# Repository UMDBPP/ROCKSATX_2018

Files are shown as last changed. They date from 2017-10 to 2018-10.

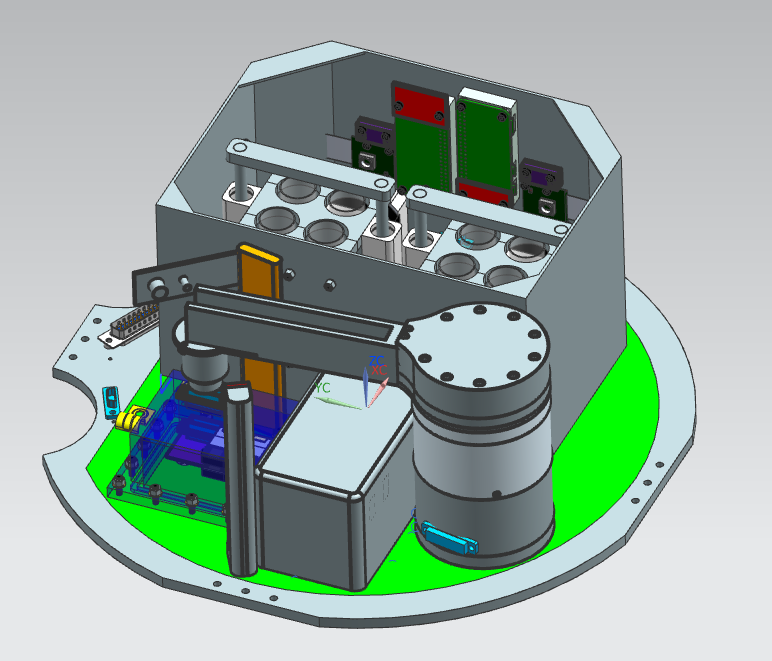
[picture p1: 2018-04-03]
CAD/CAD Renders/Opqaue Full Assembly ISTR.PNG

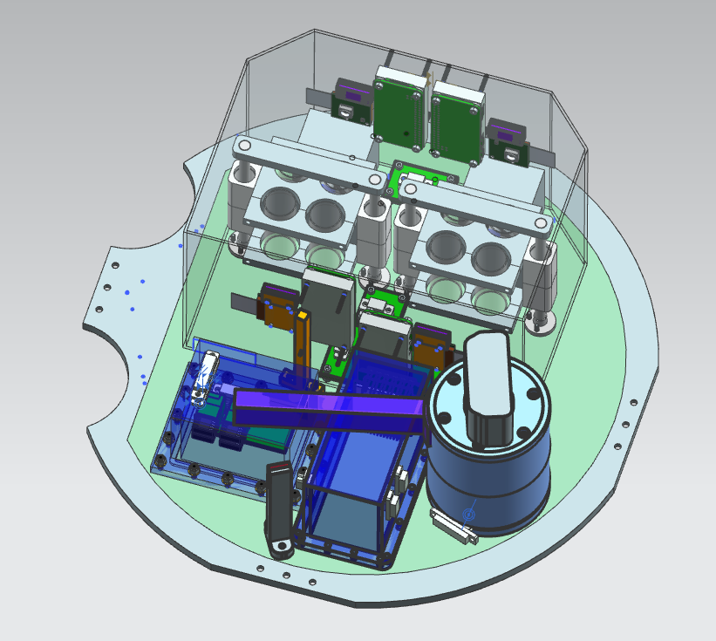
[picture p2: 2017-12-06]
CAD/CAD Renders/Full Assembly.PNG

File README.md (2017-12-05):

# ROCKSATX_2018
BPP 2018 Rocksat - X

Payload: TERP (Tribocharging Experiment and Robotic Performance)

Contains two experiments: STAR and SCAMP

## STAR
Stratification and Tribocharging Analysis of Regolith (STAR)

## SCAMP
Space Characterization and Assessment of Manipulator Performance

# Organization
CAD/: All mechanical design files (CAD)

Payload_Integration/:  Files documenting external interfaces of TERP

SCAMP/: SCAMP-specific design files

STAR/: STAR-specific design files

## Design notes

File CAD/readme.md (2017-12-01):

Top level assembly is: TERP_Payload.prt

Do not commit files with random numbers at the end. Do not use spaces in filenames.

To load assembly. 

* Open NX but not the assembly.
* Open assembly load options. Under Load, selected "From Search Folders"
* Under "Add folder to search", click browse, and select each subfolder in turn
* Click ok
* Release the assembly

This process only needs to be done on each users machine and every time a new folder is added.

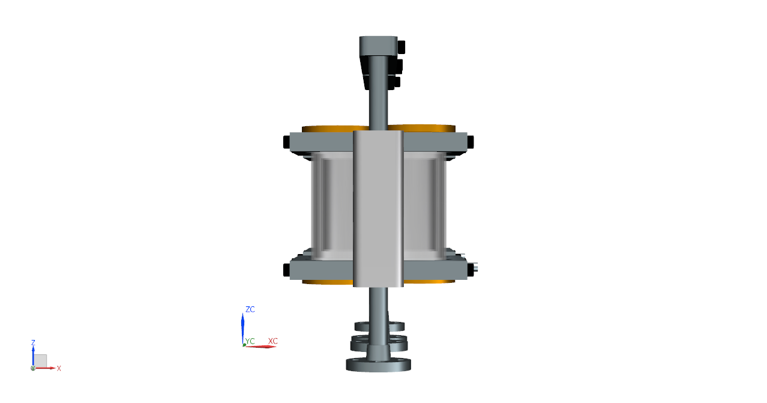
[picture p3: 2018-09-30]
CAD/CAD Renders/Shaker_rack_005.png

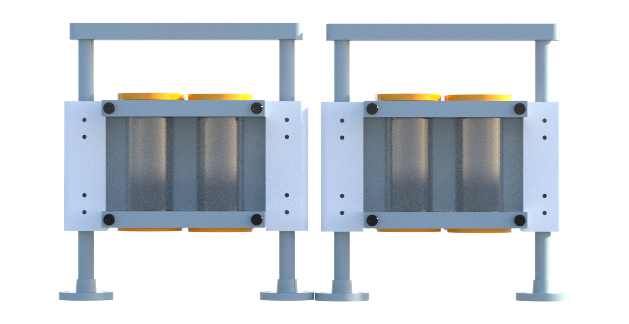
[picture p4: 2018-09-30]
CAD/CAD Renders/shaker_rack_008.png

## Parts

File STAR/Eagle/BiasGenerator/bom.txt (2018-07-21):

Partlist exported from D:/Joseph/Documents/School/College/Clubs/RockSatX/2017-2018/GIT/ROCKSATX_2018/STAR/Eagle/BiasGenerator/bias_generator.sch at 7/8/2018 3:00 PM

Qty Value             Device            Package       Parts           Description                                
2   .1uF              C-USC0603         C0603         C_GND, C_VCC    CAPACITOR, American symbol
CL10B104KB8NNNC          
1   1.5k              R-US_R2512        R2512         R_LTOUT         RESISTOR, American symbol                  
35221K5FT
1   10uF              CAPACITOR2-J-LEAD 2J-LEAD       C_LTOUT                                                    
CKG57NX7R2A106M500JH
1   1M                R-US_R0603        R0603         R_LAD1          RESISTOR, American symbol                  
ERJ-3GEYJ105V
2   1uF               CAPACITORC0603    0603          C_LTIN, C_LTREQ                                            
CL10A105KB8NNNC
2   20k               R-US_R0603        R0603         R_POT1          RESISTOR, American symbol                  
RMCF0603JT20K0
1   3269W-1-503LF     3269W-1-503LF     POTENTIOMETER R_POT2          Bourns Inc 50k Potentiometer 3269W-1-503LF 
1   33k               R-US_R0603        R0603         R_LAD2          RESISTOR, American symbol                  
1   4.7pF             CAPACITORC0603    0603          C_LAD                                                      
06032U4R7BAT2A
1   402k              R-US_R0603        R0603         R_DIV1          RESISTOR, American symbol                  
ERJ-3EKF4023V
1   52.6              R-US_R0603        R0603         R_LAD3          RESISTOR, American symbol                  
2   82nH              L-US              C0603         L_VCC, L_VOUT   INDUCTOR, American symbol                  
AIML-0603-82NK-T
1   AMC1311-Q1        AMC1311-Q1        SOIC8         ISO                                                        
1   ASPI-4020S-100M-T ASPI-4020S-100M-T 4MM           L_LT                                                       
1   DFT7160-105B      DFT7160-105B      DFT7160       CHOKE                                                      
1   J30J-9J30         J30J-9J30         ZKN-9-J30     J1                                                         
1   LT8330            LT8330            8-DFN         SWITCH                                                     
1   NCV4274ADT50RKG   NCV4274ADT50RKG   DPAK          REG                                                        
1   PMEG6010CEJ       SCHOTTKYSOD323    SOD323        D_LT

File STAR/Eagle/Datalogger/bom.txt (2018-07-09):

Partlist exported from C:/UMD/BPP/ROCKSAT X/2018/ROCKSATX_2018/STAR/Eagle/Datalogger/datalogger.sch at 7/8/2018 11:54

Qty Value        Device       Package         Parts               Description                
5   0.1uF        C-USC0603    C0603           C1, C3, C6, C7, C9  CAPACITOR, American symbol 
5   10nF         C-USC0603    C0603           C2, C4, C5, C8, C10 CAPACITOR, American symbol 
1   1M           R-US_R0603   R0603           R2                  RESISTOR, American symbol  
1   J30J-25      J30J-25      ZKN-25          J1                                             
1   MICRO_SD     MICRO_SD     MICRO_SD_HINGED U$1                                            
1   SSL.3IN_SILK SSL.3IN_SILK SSL_SILK_.3IN   GND1                                           
2   USB_A        USB_A        USB_A           U$2, U$3

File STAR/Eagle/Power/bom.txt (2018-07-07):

Partlist exported from C:/UMD/BPP/ROCKSAT X/2018/ROCKSATX_2018/STAR/Eagle/Power/Power.sch at 7/7/2018 15:11

Qty Value              Device             Package  Parts                   Description                
3   .1 uF              C-USC0603          C0603    C7, C8, C9              CAPACITOR, American symbol 
3   .18 uF             C-USC0603          C0603    C10, C11, C12           CAPACITOR, American symbol 
3   10 uF              C-USC0603          C0603    C13, C14, C15           CAPACITOR, American symbol 
3   10 uF              C-USC1210          C1210    C1, C2, C3              CAPACITOR, American symbol 
3   13.3k              R-US_R0603         R0603    R5, R7, R9              RESISTOR, American symbol  
5   1410J0500404MXTE03 1410J0500404MXTE03 1410     U$3, U$4, U$5, U$6, U$7                            
1   199.5k             R-US_R0603         R0603    R4                      RESISTOR, American symbol  
5   1nF                C-USC0603          C0603    C17, C19, C21, C23, C25 CAPACITOR, American symbol 
3   2.2 uF             C-USC1210          C1210    C4, C5, C6              CAPACITOR, American symbol 
3   23.2k              R-US_R0603         R0603    R1, R2, R3              RESISTOR, American symbol  
1   3.7u               7443551370         1365     L3                                                 
1   45.2k              R-US_R0603         R0603    R8                      RESISTOR, American symbol  
1   5.5u               744325550          1050     L2                                                 
5   744029000068       744029000068       2813     L4, L5, L6, L7, L8                                 
1   75.4k              R-US_R0603         R0603    R6                      RESISTOR, American symbol  
1   9.7u               744314101          7050     L1                                                 
2   DFT7160-105B       DFT7160-105B       DFT7160  U$1, U$2                                           
3   DO-214AC           DO-214AC           DO-214AC D1, D2, D3                                         
1   J30J-25            J30J-25            ZKN-25   J1                                                 
3   LMR16020           LMR16020           SO8      U1, U2, U3

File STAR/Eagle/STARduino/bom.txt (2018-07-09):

Partlist exported from C:/UMD/BPP/ROCKSAT X/2018/ROCKSATX_2018/STAR/Eagle/STARduino/starduino.sch at 7/8/2018 9:45

Qty Value                   Device                 Package         Parts                                                    Description                MANUFACTURER_PART_NUMBER VENDOR           
1                           JUMPER-2PTH            1X02            JP2                                                      Jumper                                                               
1                           PINHD-2X3              2X03            JP3                                                      PIN HEADER                                                           
1                           PINHD-2X5              2X05            JP1                                                      PIN HEADER                                                           
13  100nF                   C-USC0603              C0603           C1, C2, C3, C4, C7, C8, C9, C12, C13, C14, C16, C18, C20 CAPACITOR, American symbol                                           
1   100pF                   C-USC0603              C0603           C19                                                      CAPACITOR, American symbol                                           
2   10k                     R-US_R0603             R0603           R1, R2                                                   RESISTOR, American symbol                                            
2   10uF                    C-USC0603              C0603           C6, C15                                                  CAPACITOR, American symbol                                           
1   1nF                     C-USC0603              C0603           C17                                                      CAPACITOR, American symbol                                           
1   1uF                     C-USC0603              C0603           C5                                                       CAPACITOR, American symbol                                           
1   220k                    R-US_R0603             R0603           R8                                                       RESISTOR, American symbol                                            
1   220nF                   C-USC0603              C0603           C21                                                      CAPACITOR, American symbol                                           
1   3.6k                    R-US_R0603             R0603           R5                                                       RESISTOR, American symbol                                            
1   330                     R-US_R0603             R0603           R4                                                       RESISTOR, American symbol                                            
3   4.7k                    R-US_R0603             R0603           R3, R9, R10                                              RESISTOR, American symbol                                            
1   4.7k                    RESISTOR-ARRAY0603-ARV 0603-ARV        R7                                                       Array Chip Resistor                                                  
1   6.8k                    R-US_R0603             R0603           R6                                                       RESISTOR, American symbol                                            
2   6.8pF                   C-USC0603              C0603           C10, C11                                                 CAPACITOR, American symbol                                           
1   ABS07AIG-32.768KHZ-1-T  ABS07AIG-32.768KHZ-1-T 2-SMD           XTAL1                                                                                                                         
1   ADXL375BCCZ             ADXL375BCCZ            LGA-14          U8                                                                                                                            
1   ATSAMD21G18             ATSAMD21G18            48-TQFP         U2                                                                                                                            
2   BLM18KG221BH1D          FERRITE_BEAD-0603      0603            FB1, FB2                                                                                                                      
1   BMX055                  BMX055                 LGA-20          U7                                                                                                                            
1   CC2                     CC2                    CC2             U11                                                                                                                           
1   CR1025                  CR1025                 CR1025          B1                                                                                                                            
1   DS3231MZ+               DS3231MZ+              SOIC-8          U5                                                                                                                            
1   FODM8061-D              FODM8061-D             SO5             U$1                                                                                                                           
1   J30J-9J30J              J30J-9J30J             ZKN-9           J1                                                                                                                            
1   MAX31725MTA+            MAX31725MTA+           DFN-8           U3                                                                                                                            
1   MC14504BDTG             MC14504BDTG            TSSOP16         U6                                                                                                                            
1   MC74VHC1GT125           MC74VHC1GT125          SC-70-5         U4                                                                                                                            
1   PCA9306DCT              PCA9306DCT             SSOP8           U10                                                                                                                           
1   PCA9515A                PCA9515A               TSSOP8          U1                                                                                                                            
1   SSCMNNN015PA2A3         SSCMNNN015PA2A3        HSC-SMT-8       U12                                                                                                                           
1   SSL.3IN_SILK            SSL.3IN_SILK           SSL_SILK_.3IN   IMAG1                                                                                                                         
1   STAR                    STAR                   STAR_.3IN       IMAG2                                                                                                                         
1   TCA9535_RTW_24          TCA9535_RTW_24         RTW24_2P45X2P45 U9                                                                                  tca9535_rtw_24           Texas Instruments

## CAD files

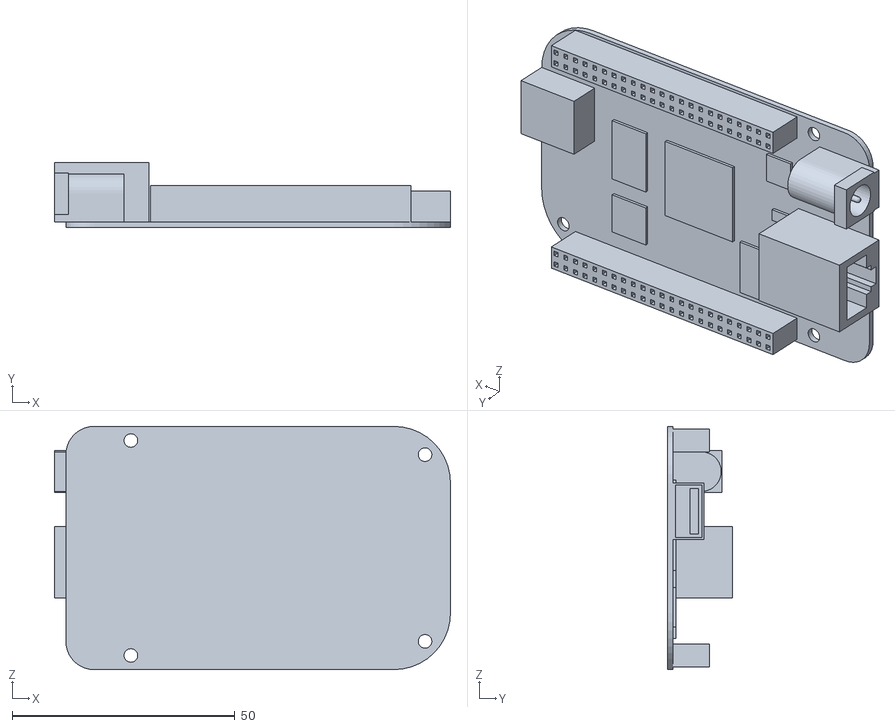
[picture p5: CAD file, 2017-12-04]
CAD/Beaglebone.stl
88.9 x 14.6 x 54.6

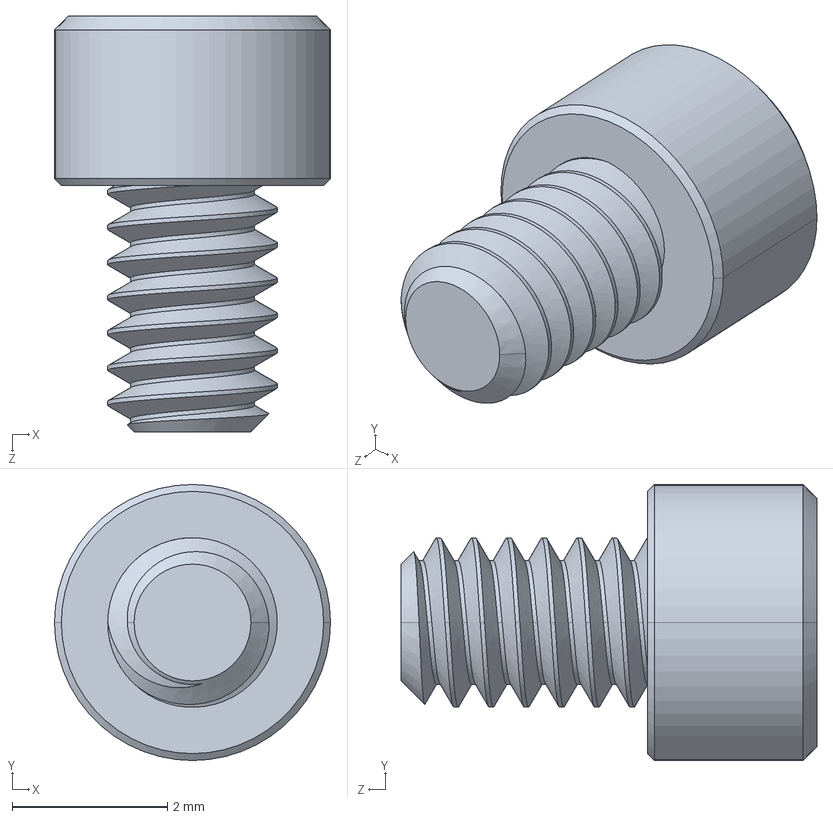
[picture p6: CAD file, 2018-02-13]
CAD/SCAMP V4.1/074.STEP
3.56 x 3.56 x 5.36 mm

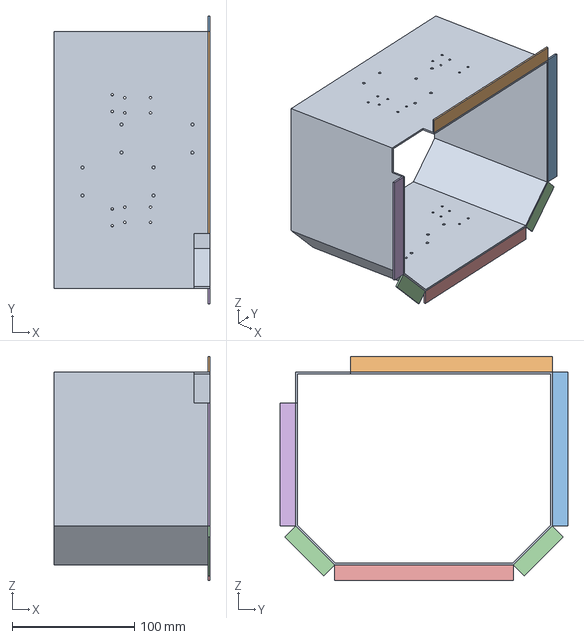
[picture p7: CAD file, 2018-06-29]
CAD/STEP/new_sunshade.stp
127.0 x 235.0 x 182.9 mm

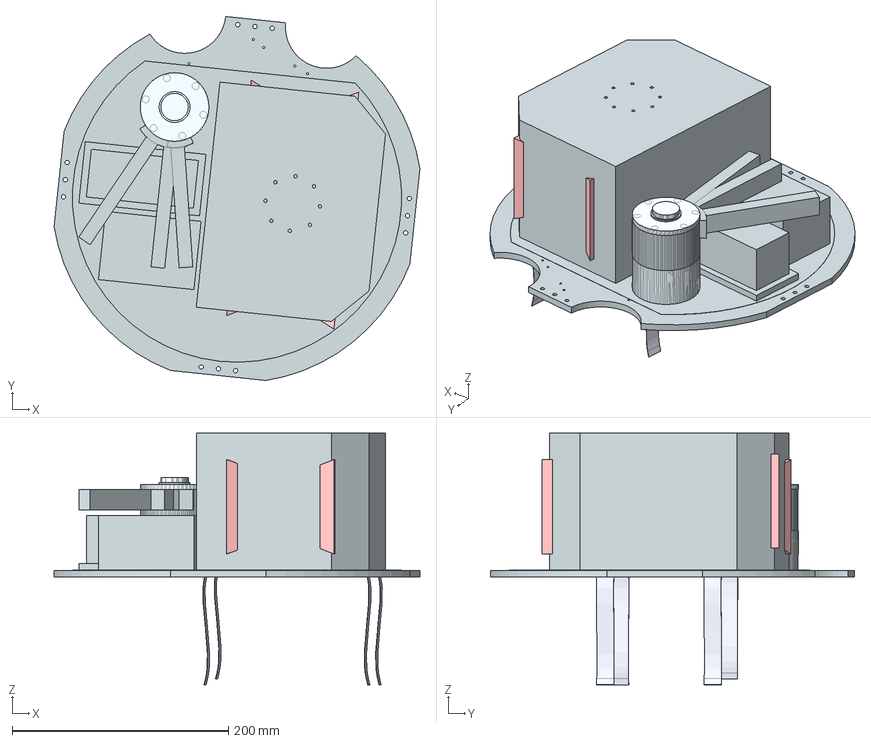
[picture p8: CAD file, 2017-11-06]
CAD/PDR_Plate_Layout.stp
338.7 x 337.0 x 233.0 mm
Electronics Box V2503
OVA5647_Lens_FOV x 4
newerbox448
new sunshade363486
PayloadSA218485
BasePlate (1)484
bearing holder473 x 8
tubeholderbase2472 x 2
test_tube482 x 8
slide rod481 x 4
rod_holder480 x 2
End Effector V3479 x 3
Pitch Motor Housing V281478 x 2
Motor End Cover444 x 2
Central Housing445 x 2
siliconbacking x 4
OVA5647_Pigtail486 x 4
OVA5647_IR-Glas485 x 4
OVA5647_Housing484 x 4
OVA5647483 x 4
RasPi_Camera_Board489 x 4
holderhalf2464 x 6
holderhalf463 x 2
link_arm x 2
shaker_disk x 2
Shaker_motor x 2

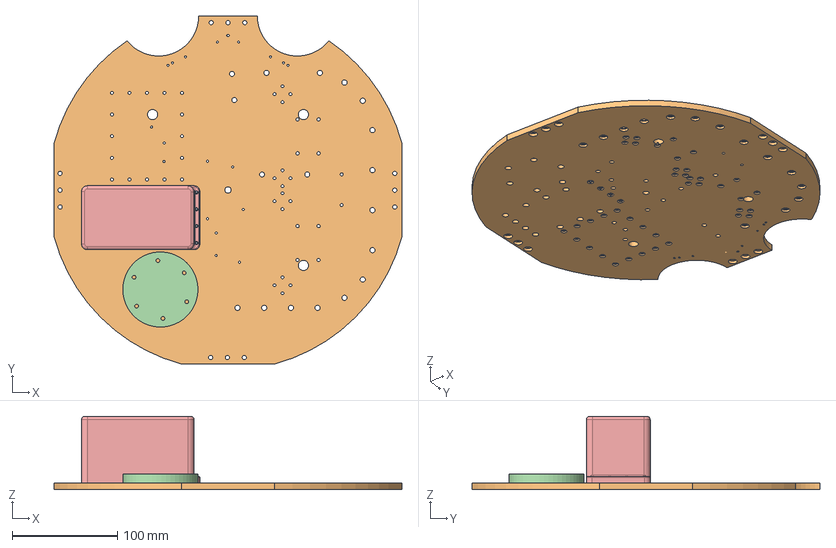
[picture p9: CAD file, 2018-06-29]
CAD/STEP/BasePlate2.stp
331.2 x 331.2 x 69.7 mm
106_step x 4

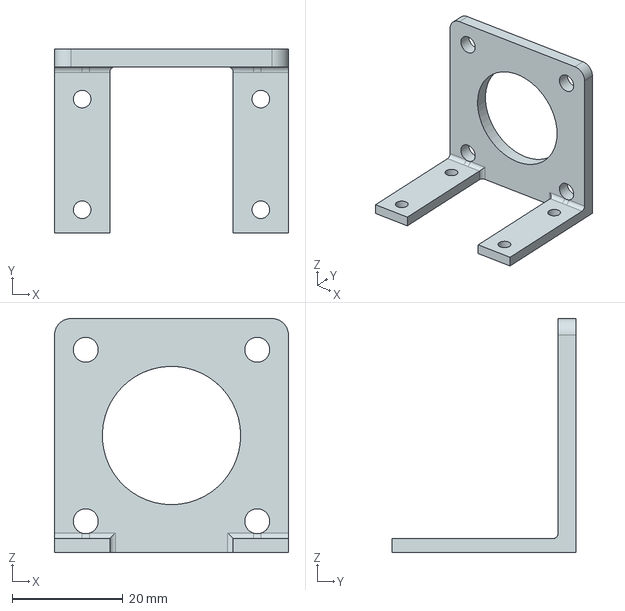
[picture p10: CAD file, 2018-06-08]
CAD/STEP/motor holder.stp
42.3 x 33.2 x 42.3 mm

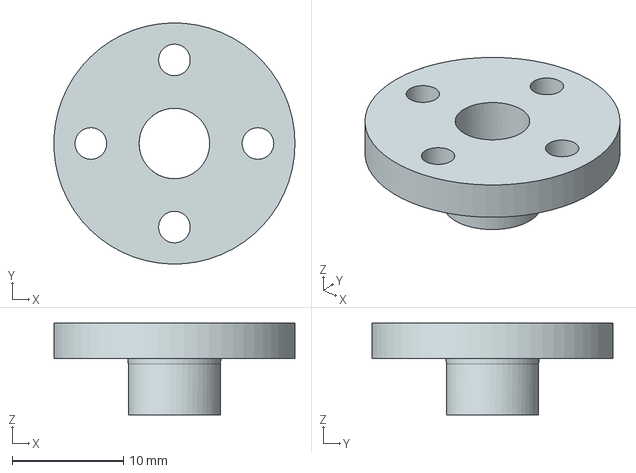
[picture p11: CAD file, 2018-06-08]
CAD/STEP/rod_baseimp.stp
21.7 x 21.7 x 8.26 mm

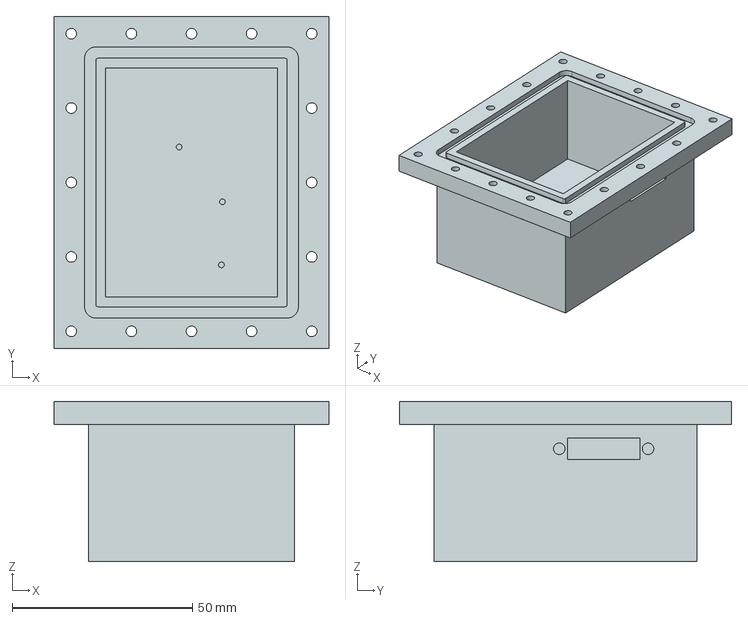
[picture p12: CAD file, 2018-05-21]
CAD/STEP/newerbox.stp
76.2 x 92.1 x 44.4 mm

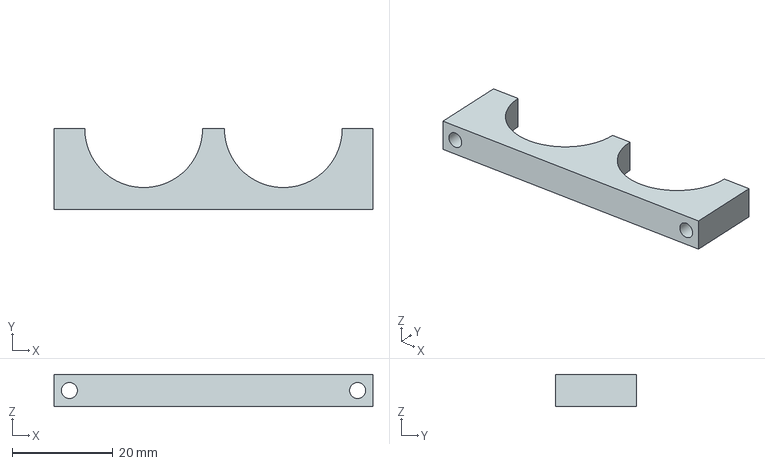
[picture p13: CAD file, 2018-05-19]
CAD/STEP/holderhalf_bottom.stp
63.2 x 16.0 x 6.35 mm

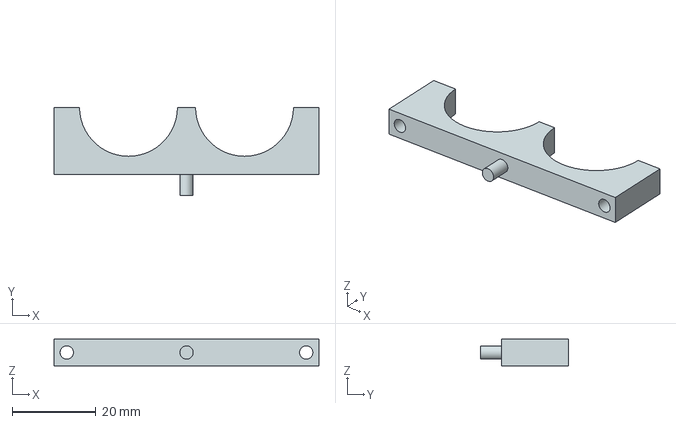
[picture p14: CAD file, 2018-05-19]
CAD/STEP/holderhalf_top.stp
63.2 x 21.1 x 6.35 mm

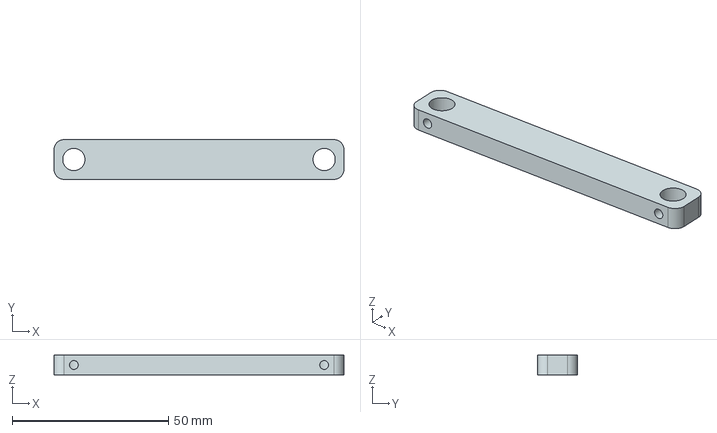
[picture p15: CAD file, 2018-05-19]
CAD/STEP/rod_holder.stp
92.7 x 12.7 x 6.35 mm

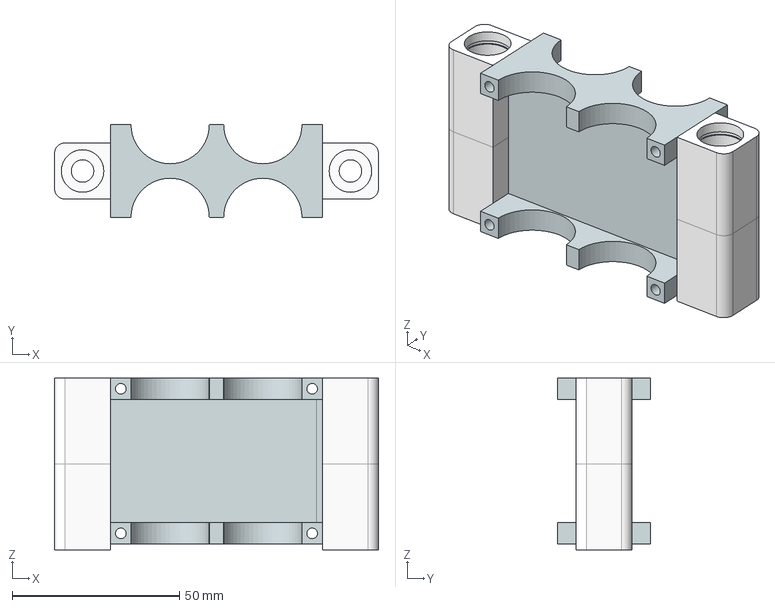
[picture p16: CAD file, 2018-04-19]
CAD/STEP/tubeholder.stp
96.8 x 27.7 x 51.3 mm
bearing_holder x 4
tubeholderbase

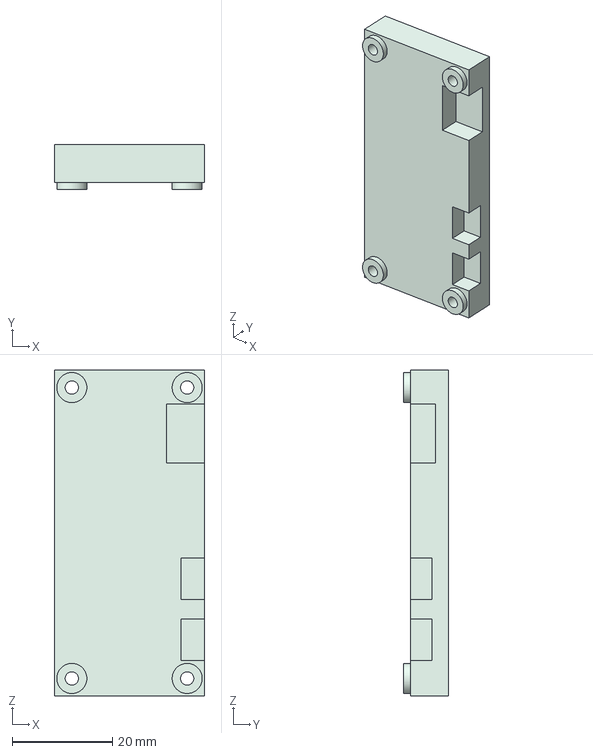
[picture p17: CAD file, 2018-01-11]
CAD/STEP/Pi_Heat_Block.stp
30.0 x 9.04 x 65.0 mm

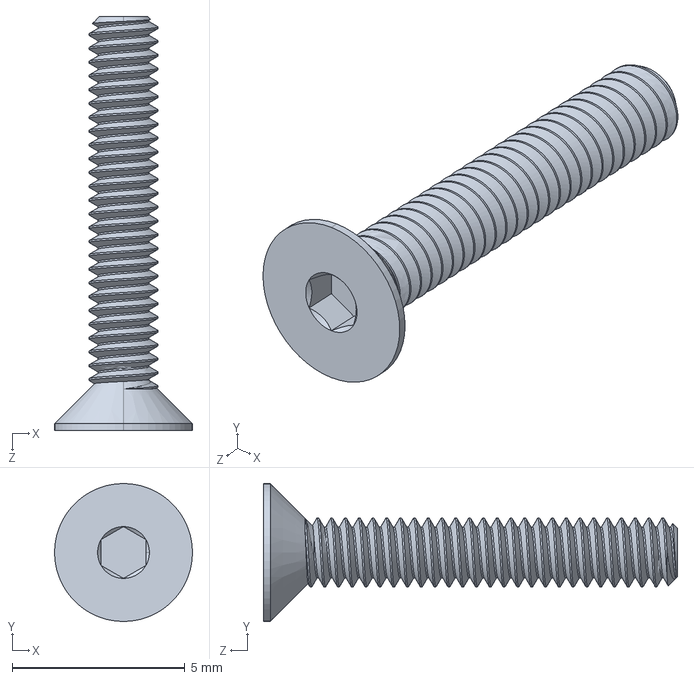
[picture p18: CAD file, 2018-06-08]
CAD/Fasteners/92125A058_TYPE 18-8 SS FLAT-HEAD SOCKET CAP SCREW.STEP
4.00 x 4.00 x 12.0 mm

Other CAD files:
CAD/SCAMP V4.1/Rough BeagleBone Black.STL
CAD/STEP/BasePlate.stp
CAD/BasePlate.prt
CAD/BasePlate_designarea.prt
CAD/Boards/BiasGenBoard.prt
CAD/Boards/BiasGenBoardAssembly.prt
CAD/Boards/Datalogger/USB.prt
CAD/Boards/LED/LED_Board.prt
CAD/Boards/MotorDriverBoard.prt
CAD/Boards/MotorDriverBoardAssembly.prt
CAD/Boards/PocketBeagle_step.prt
CAD/Boards/Starduino.prt
CAD/Boards/StarduinoAssembly.prt
CAD/Boards/datalogger.prt
CAD/Boards/datalogger_board.prt
CAD/Boards/picam/OVA5647_FOV.prt
CAD/Boards/picam/OVA5647_Housing.prt
CAD/Boards/picam/OVA5647_IC.prt
CAD/Boards/picam/OVA5647_IR-Glass.prt
CAD/Boards/picam/OVA5647_Lens_FOV.prt
CAD/Boards/picam/OVA5647_Pigtail.prt
CAD/Boards/picam/newFOV.prt
CAD/CAM/EBox.f3d
CAD/CAM/Pi_Heatsink.f3d
CAD/CAM/bottom_holder.f3d
CAD/CAM/motor_holder.f3d
CAD/CAM/rod_holder.f3d
CAD/CAM/slide_holder.f3d
CAD/CAM/top_holder.f3d
CAD/CAM/tubeholder.f3d
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

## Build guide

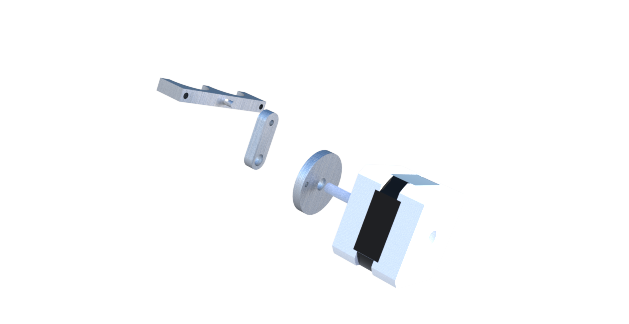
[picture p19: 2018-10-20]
CAD/CAD Renders/shaker_motor_assembly_002.png

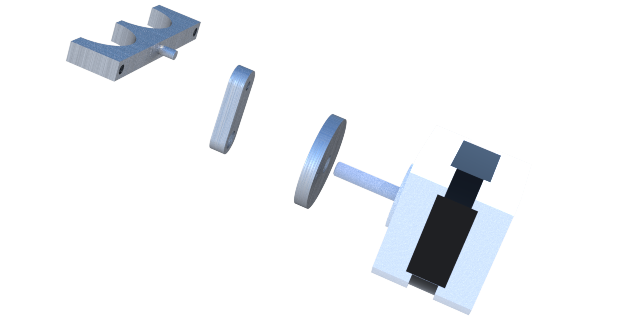
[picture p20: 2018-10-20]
CAD/CAD Renders/shaker_motor_assembly_004.png

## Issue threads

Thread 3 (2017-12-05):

Filepath with spaces in it

ascended121, 2017-12-05:
Please avoid using file paths with spaces in them because it makes it more complicated to interact with the repo via command line.

ROCKSATX_2018/CAD/SCAMP V4.1/ should be renamed to ROCKSATX_2018/CAD/SCAMP_V4.1/ if that folder is necessary

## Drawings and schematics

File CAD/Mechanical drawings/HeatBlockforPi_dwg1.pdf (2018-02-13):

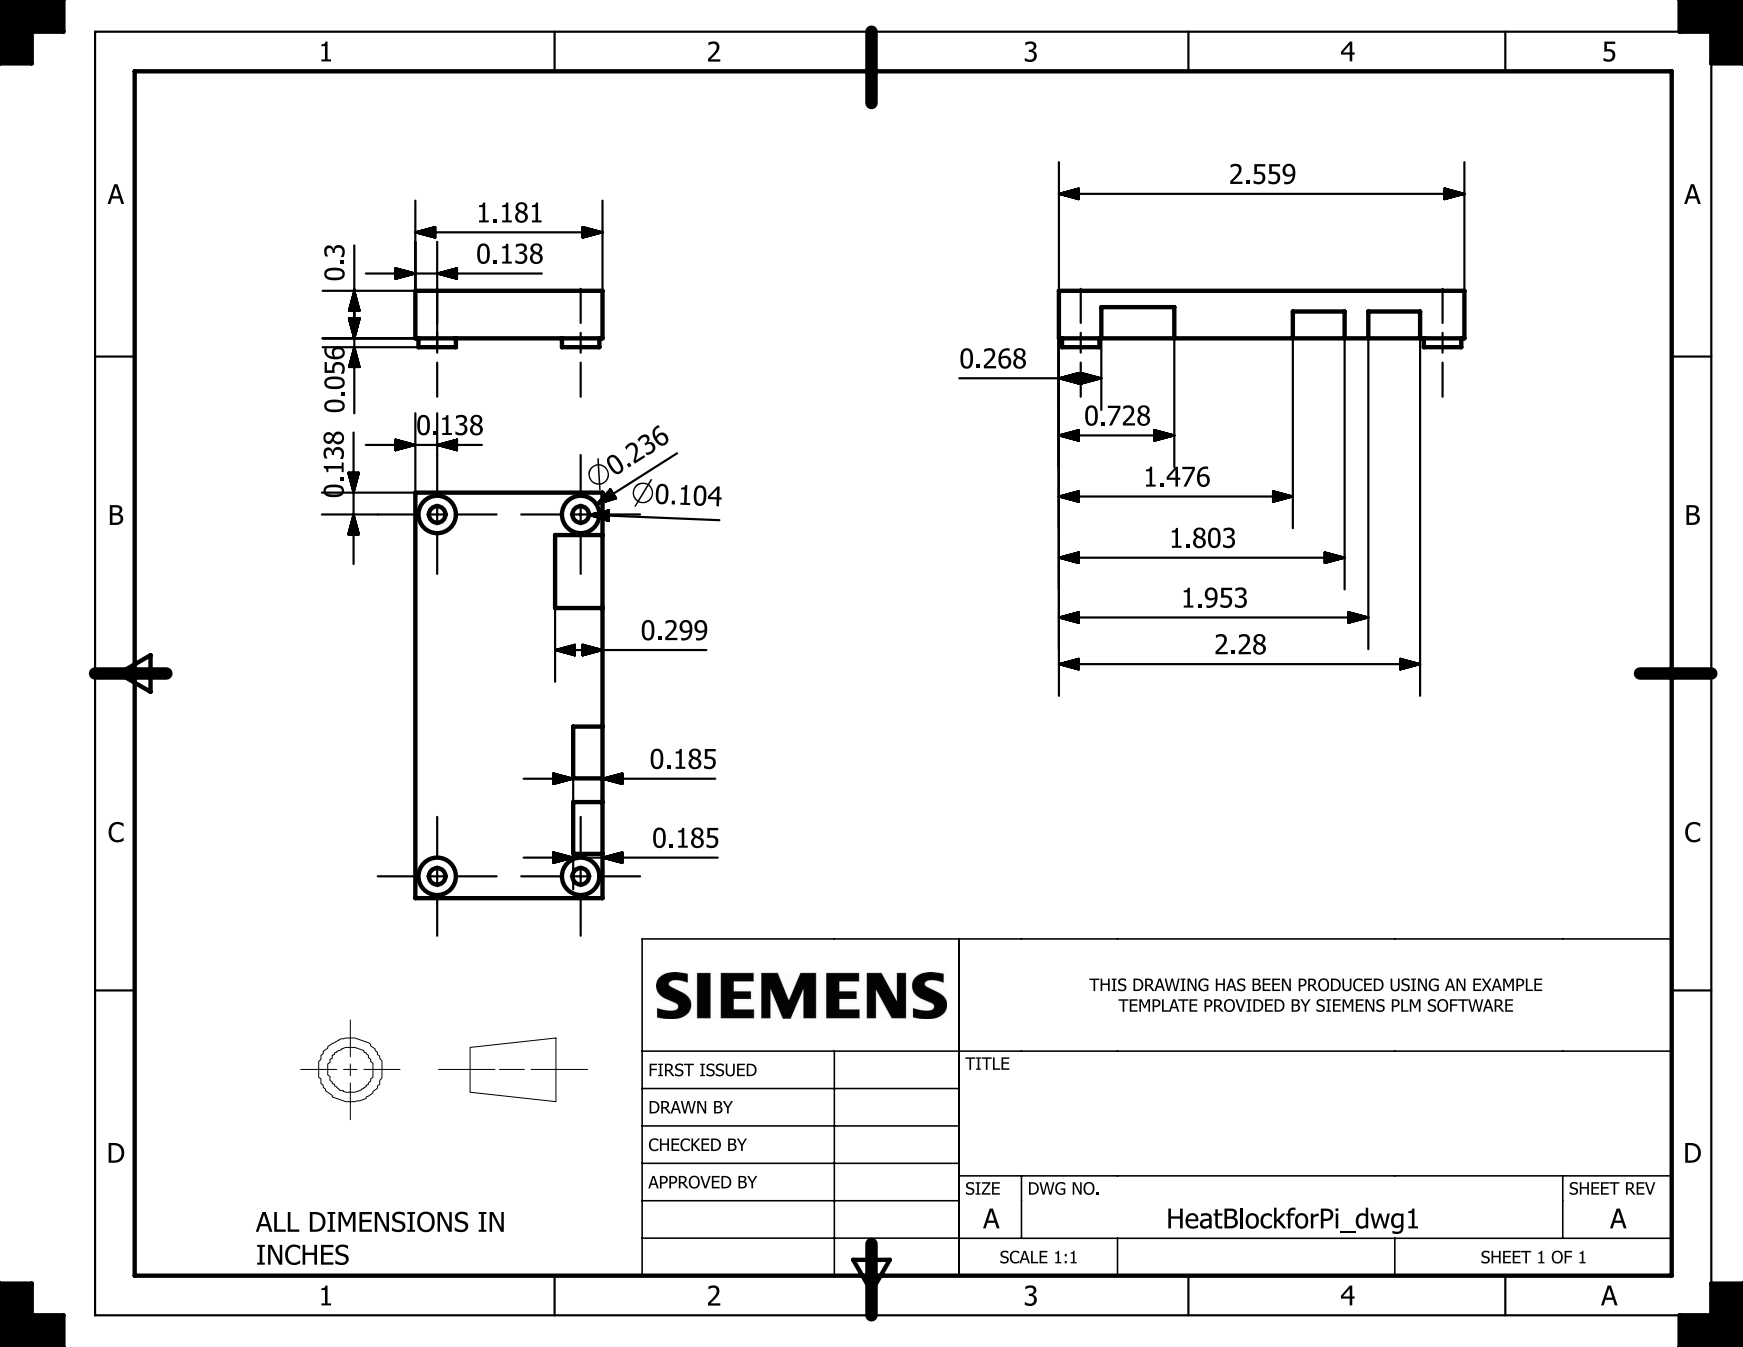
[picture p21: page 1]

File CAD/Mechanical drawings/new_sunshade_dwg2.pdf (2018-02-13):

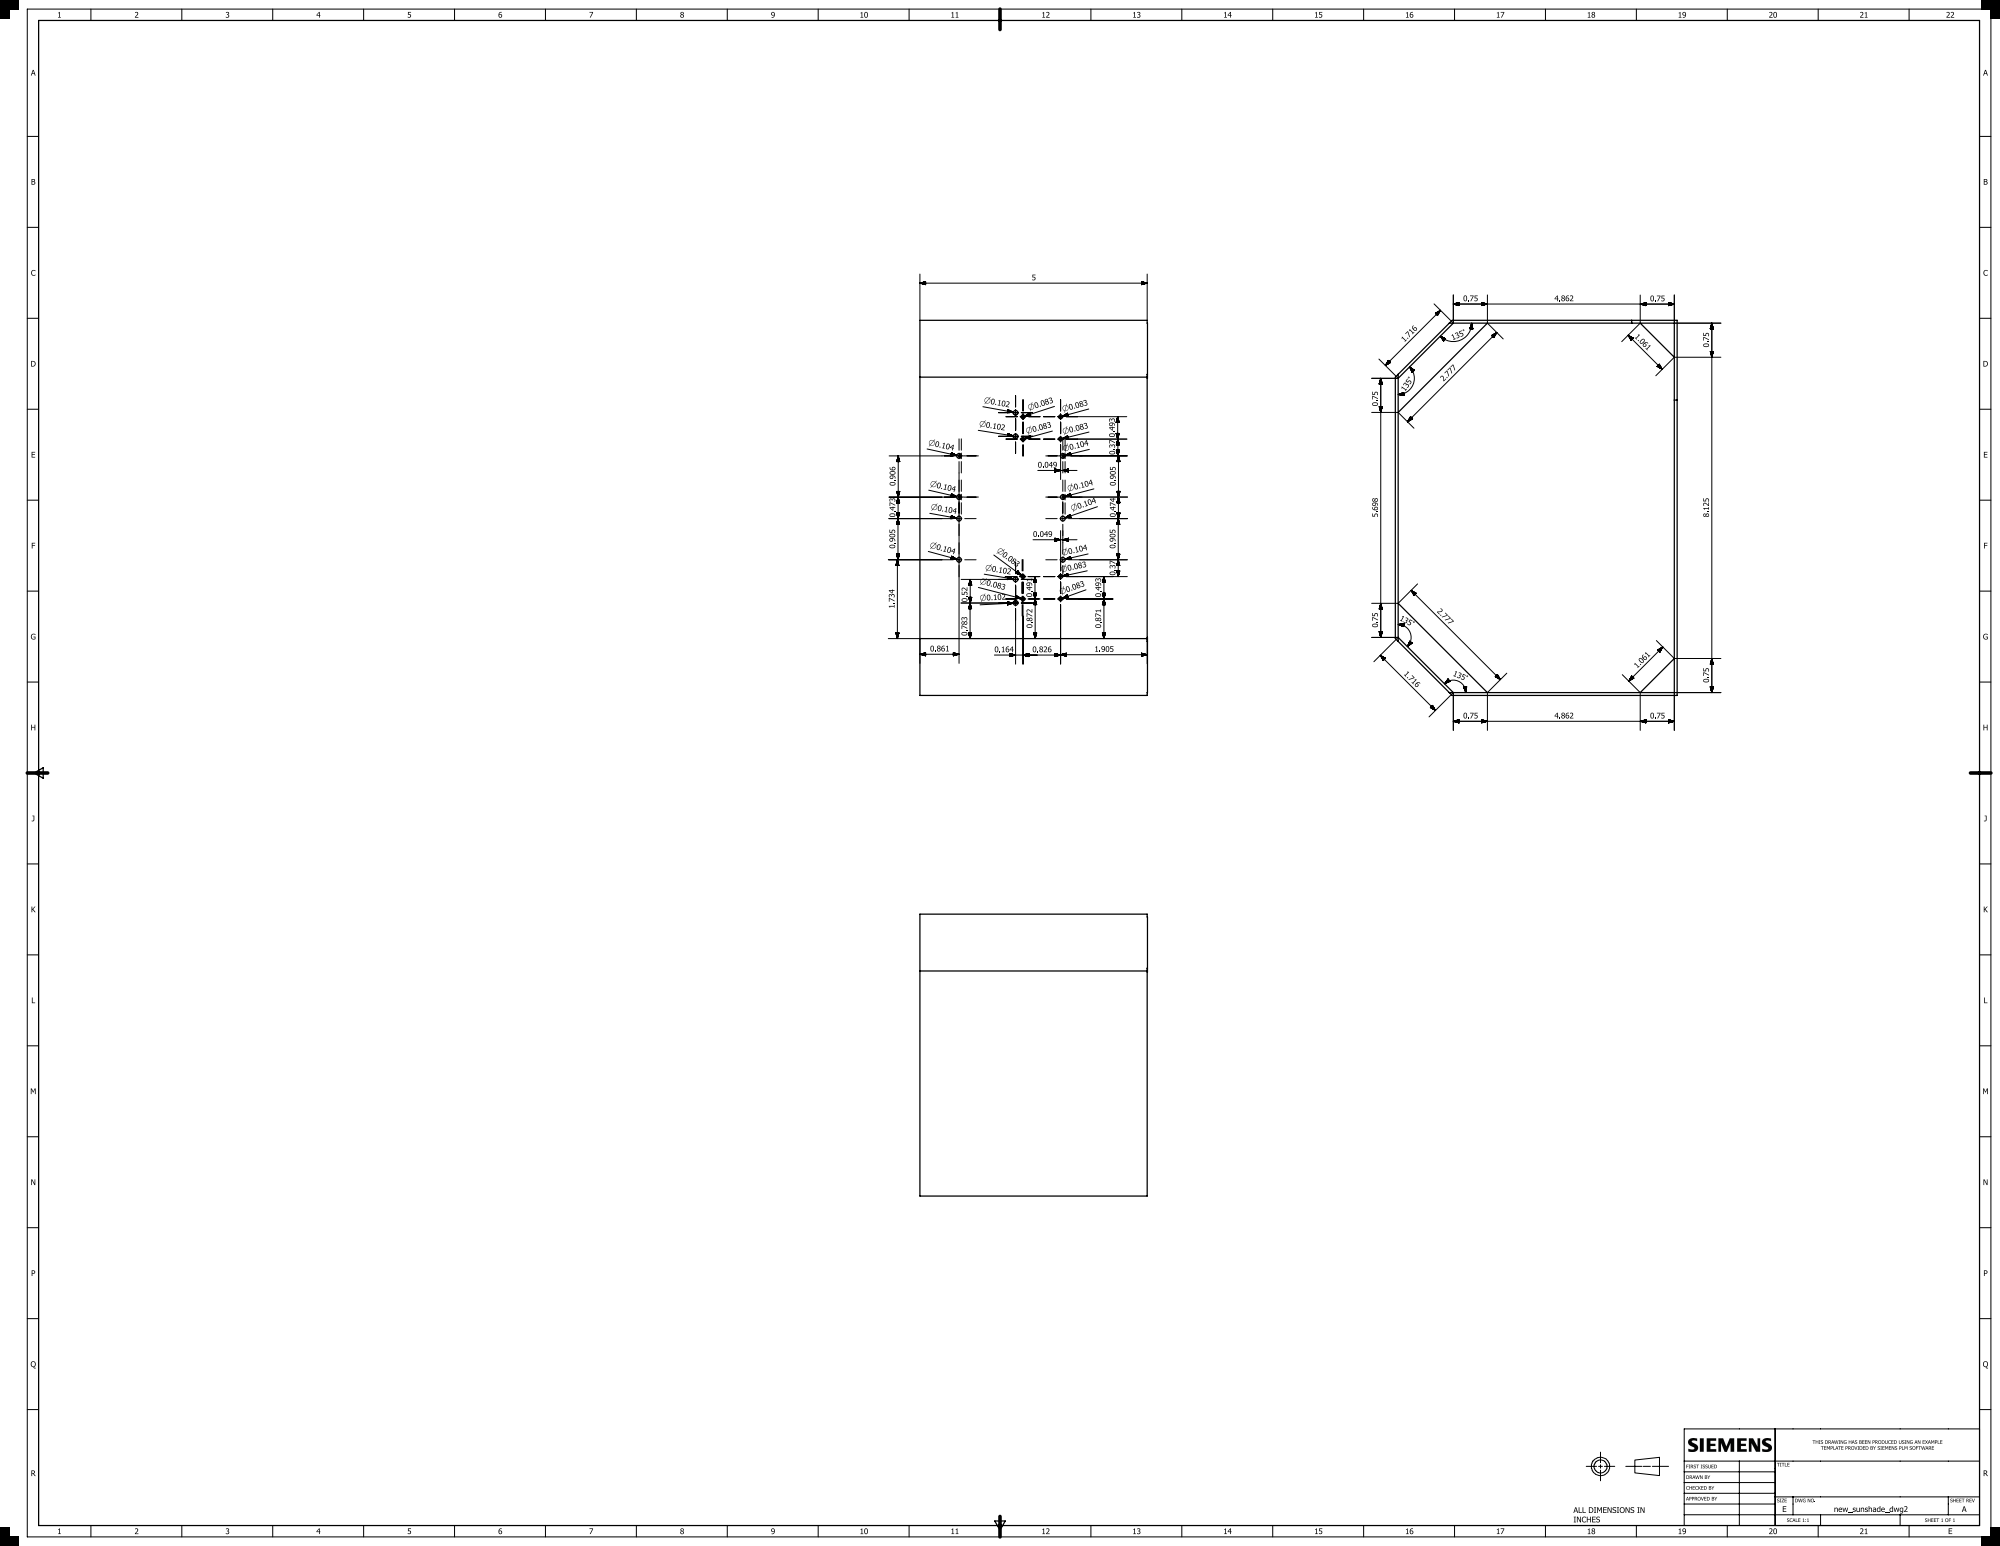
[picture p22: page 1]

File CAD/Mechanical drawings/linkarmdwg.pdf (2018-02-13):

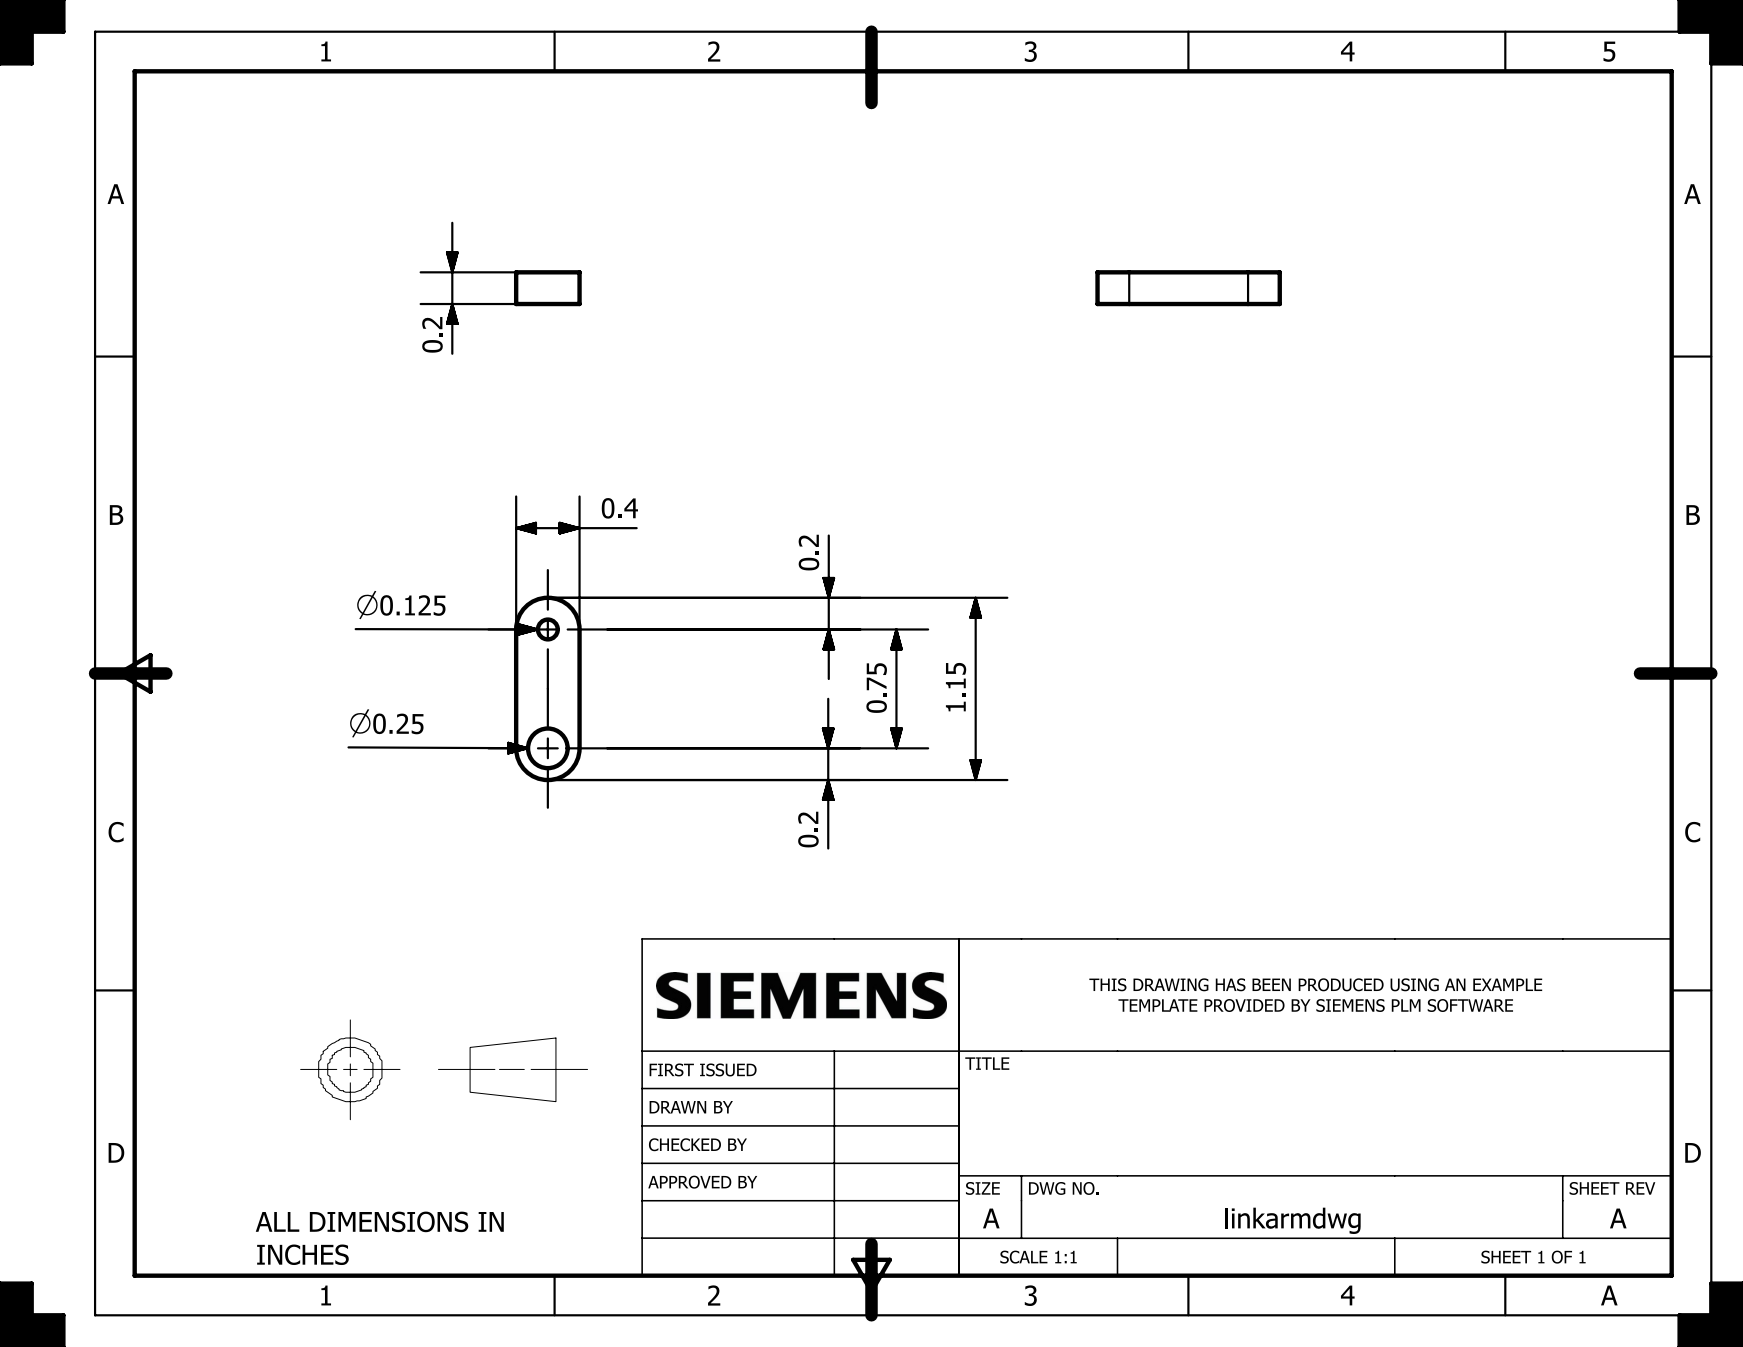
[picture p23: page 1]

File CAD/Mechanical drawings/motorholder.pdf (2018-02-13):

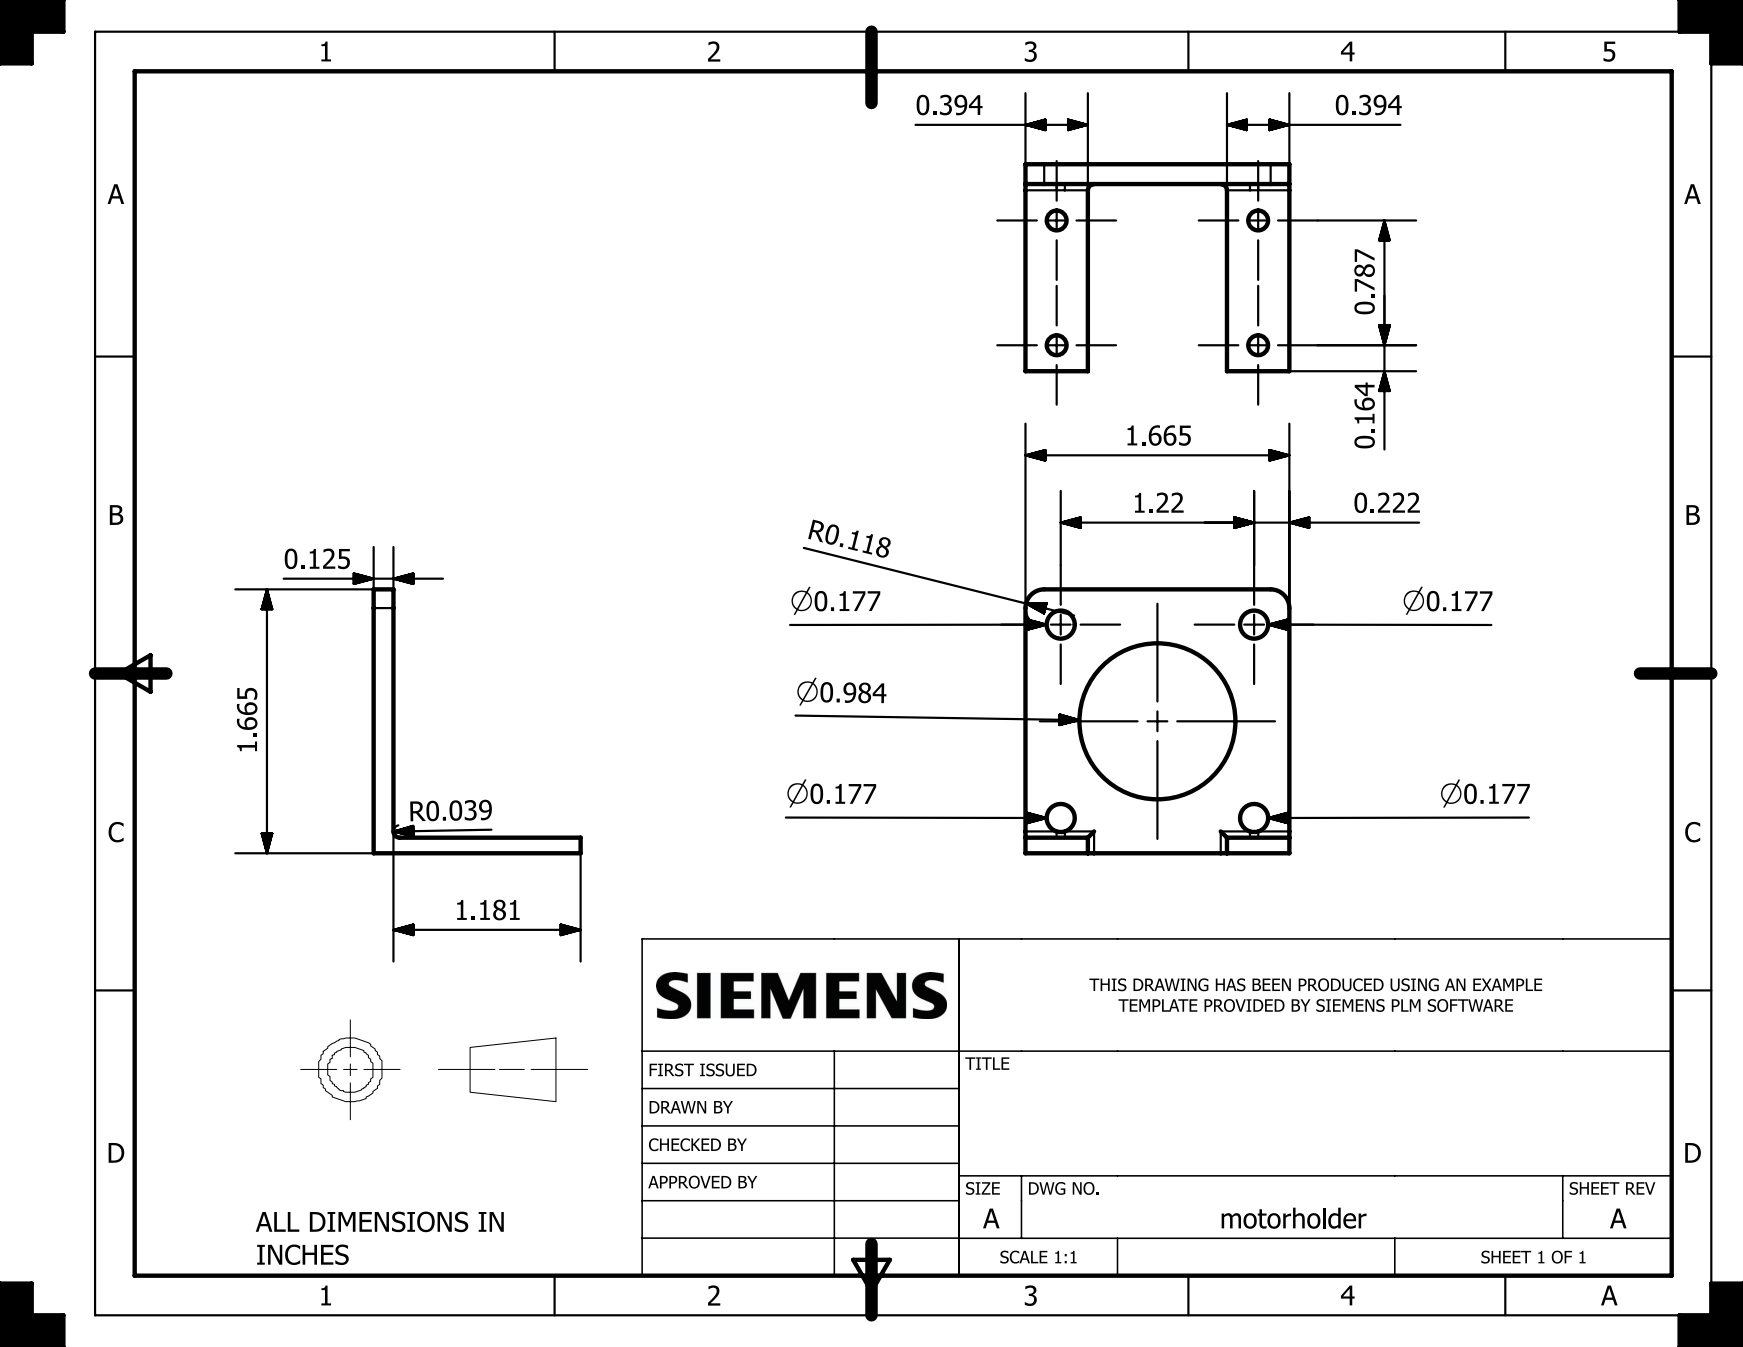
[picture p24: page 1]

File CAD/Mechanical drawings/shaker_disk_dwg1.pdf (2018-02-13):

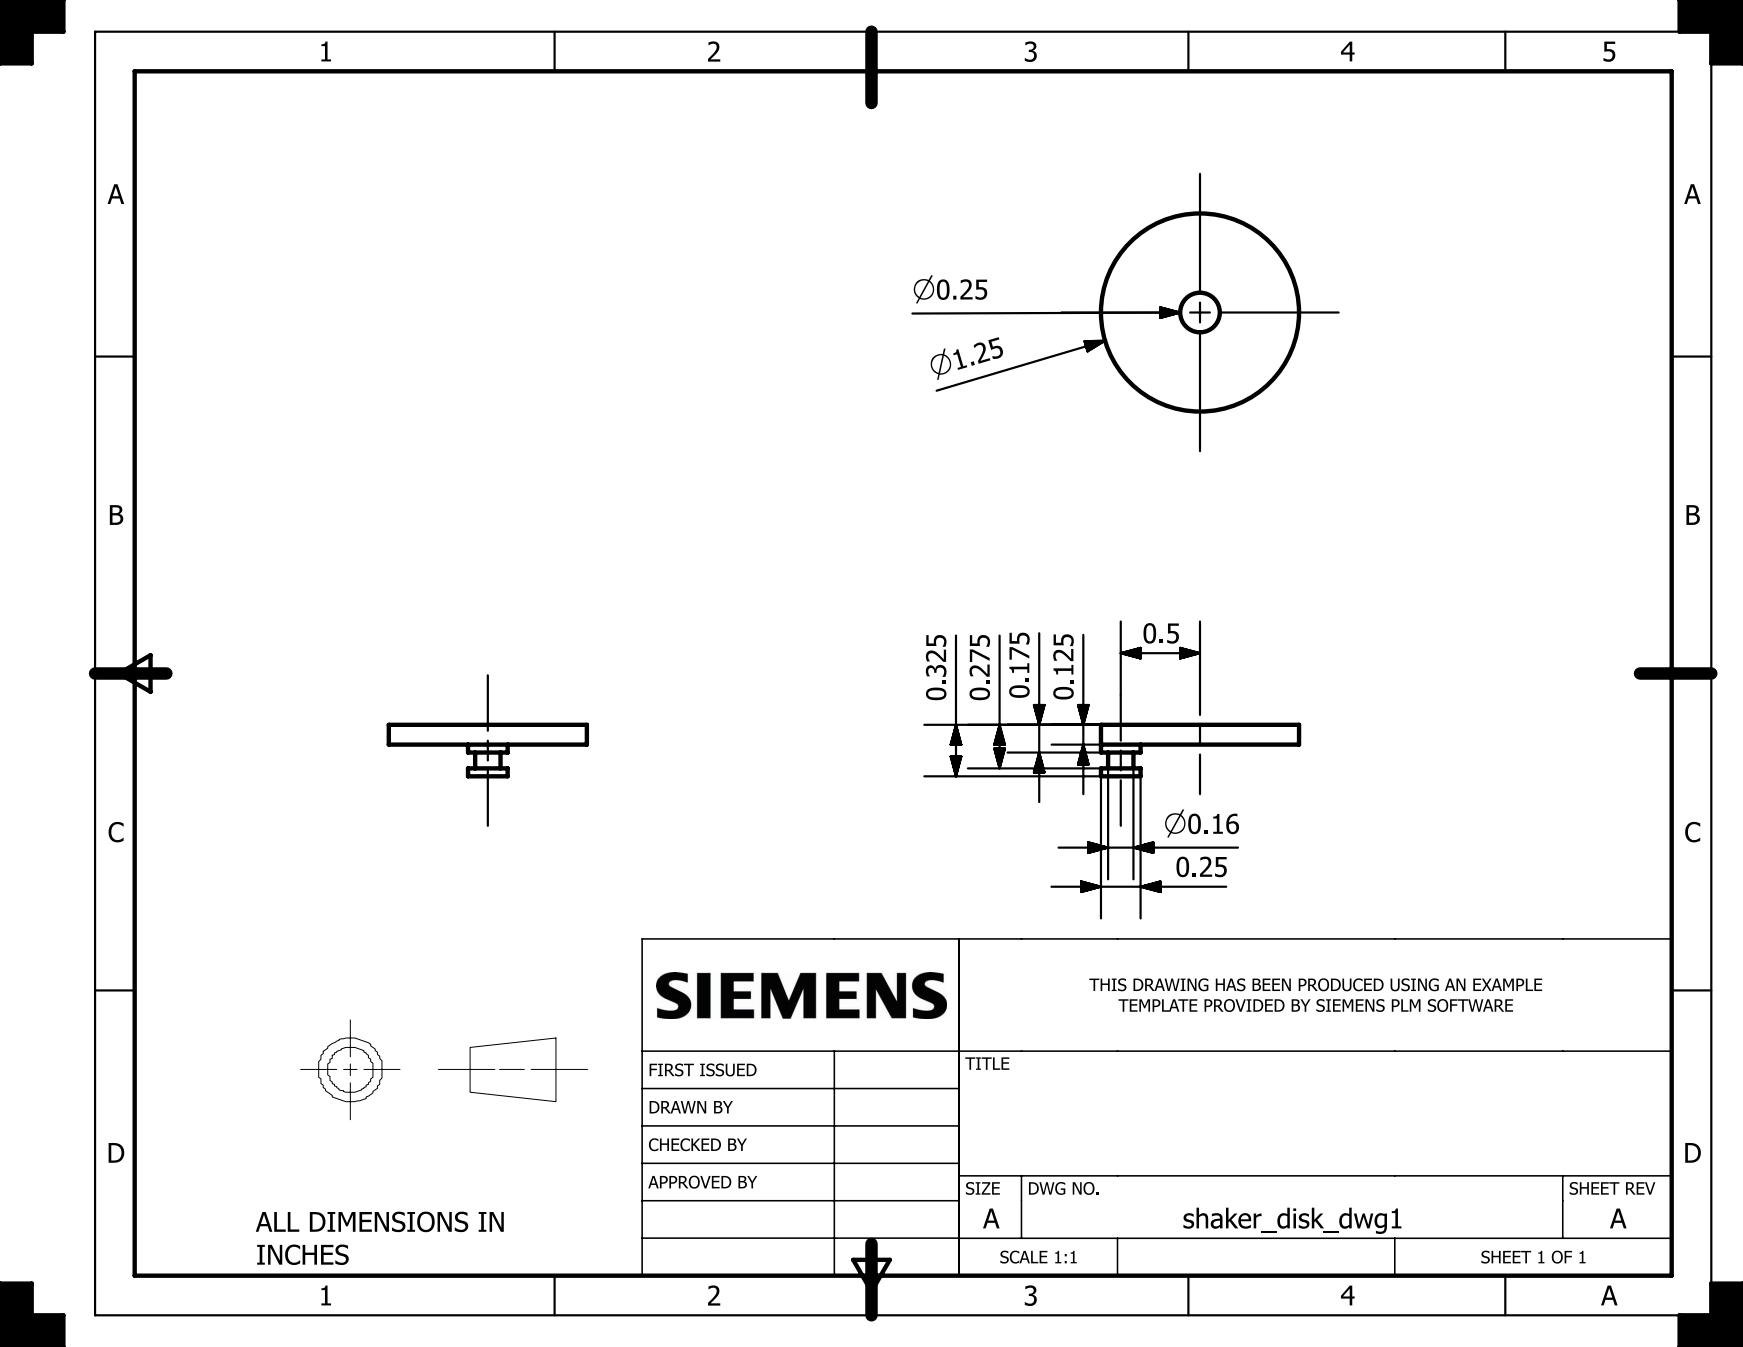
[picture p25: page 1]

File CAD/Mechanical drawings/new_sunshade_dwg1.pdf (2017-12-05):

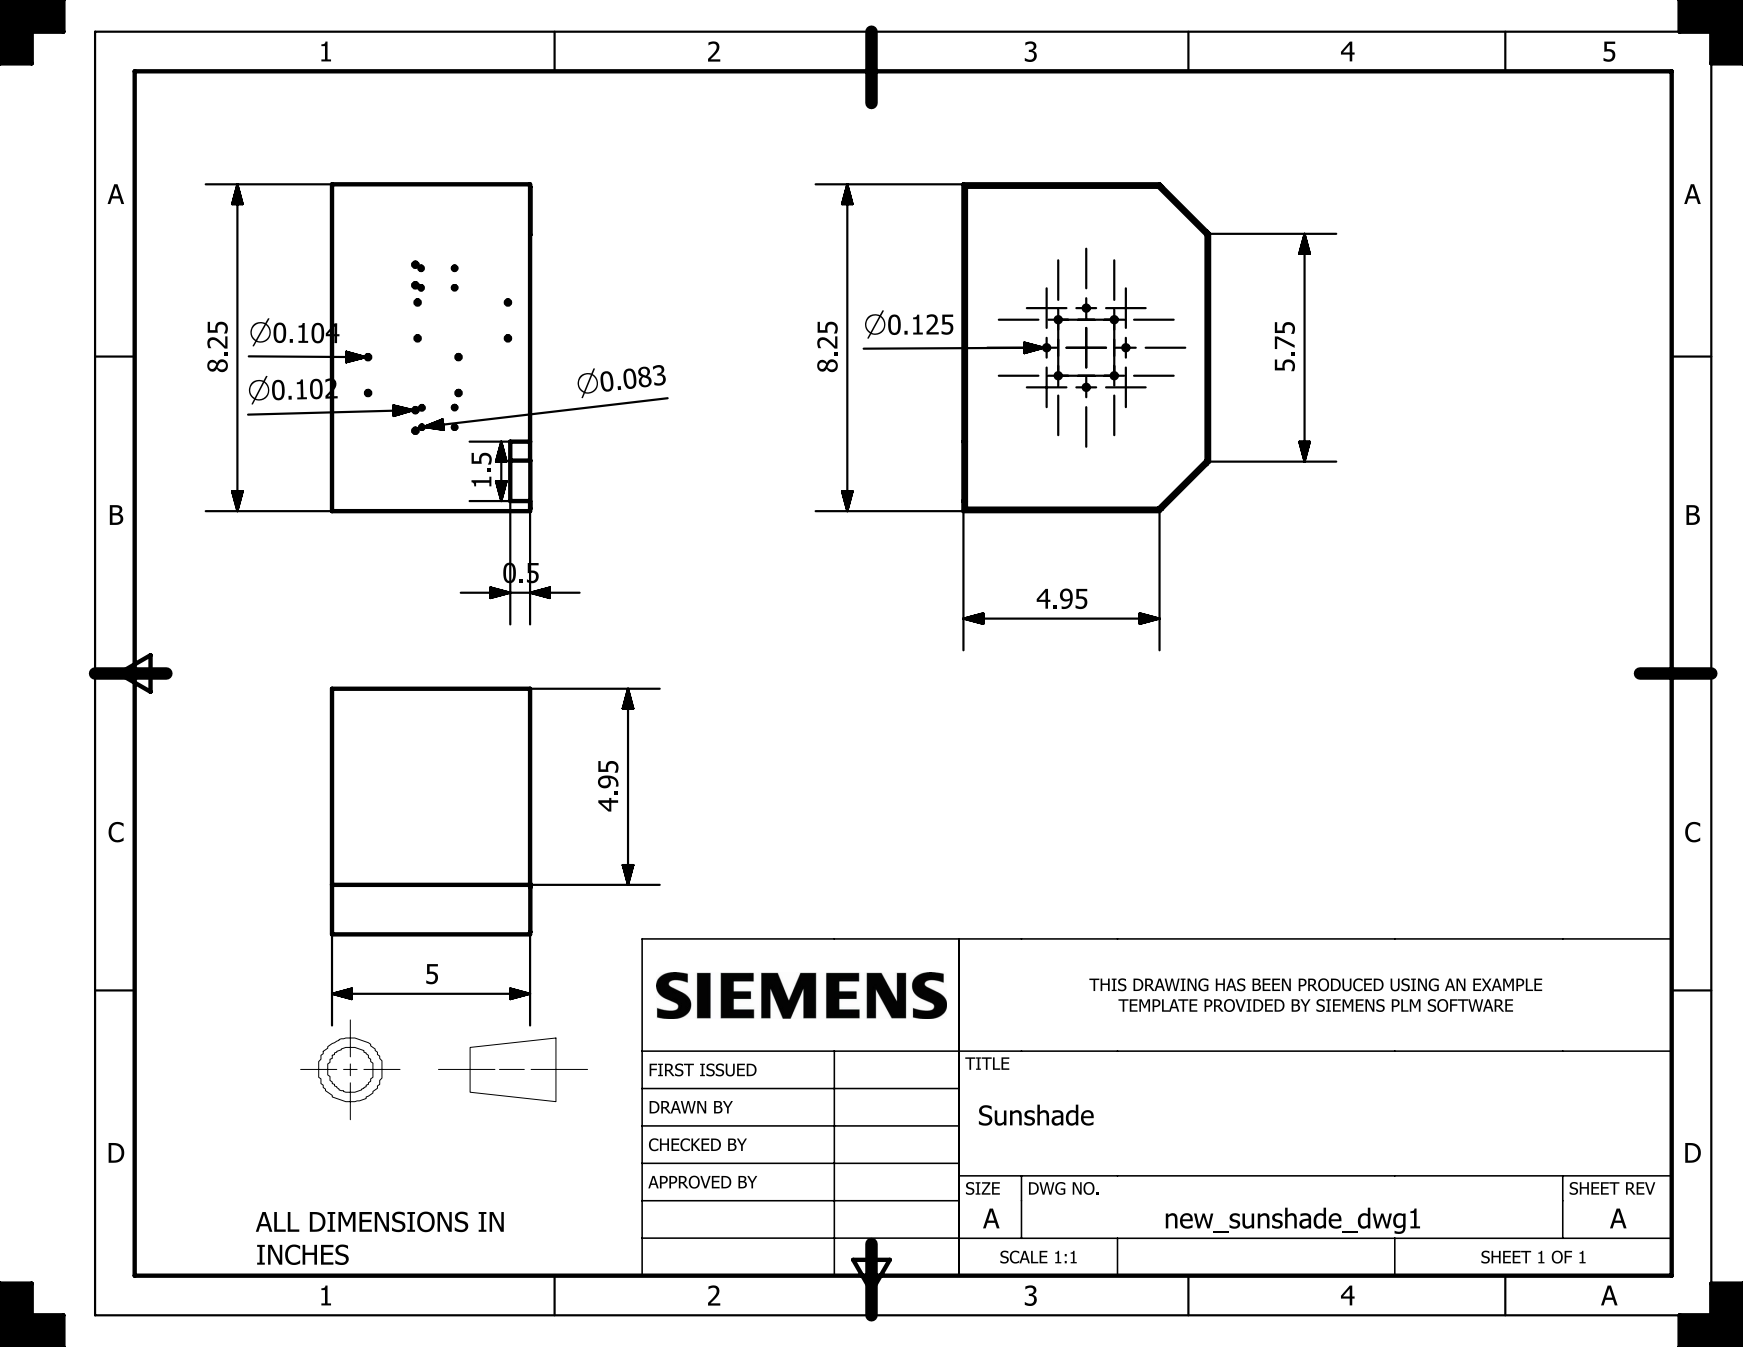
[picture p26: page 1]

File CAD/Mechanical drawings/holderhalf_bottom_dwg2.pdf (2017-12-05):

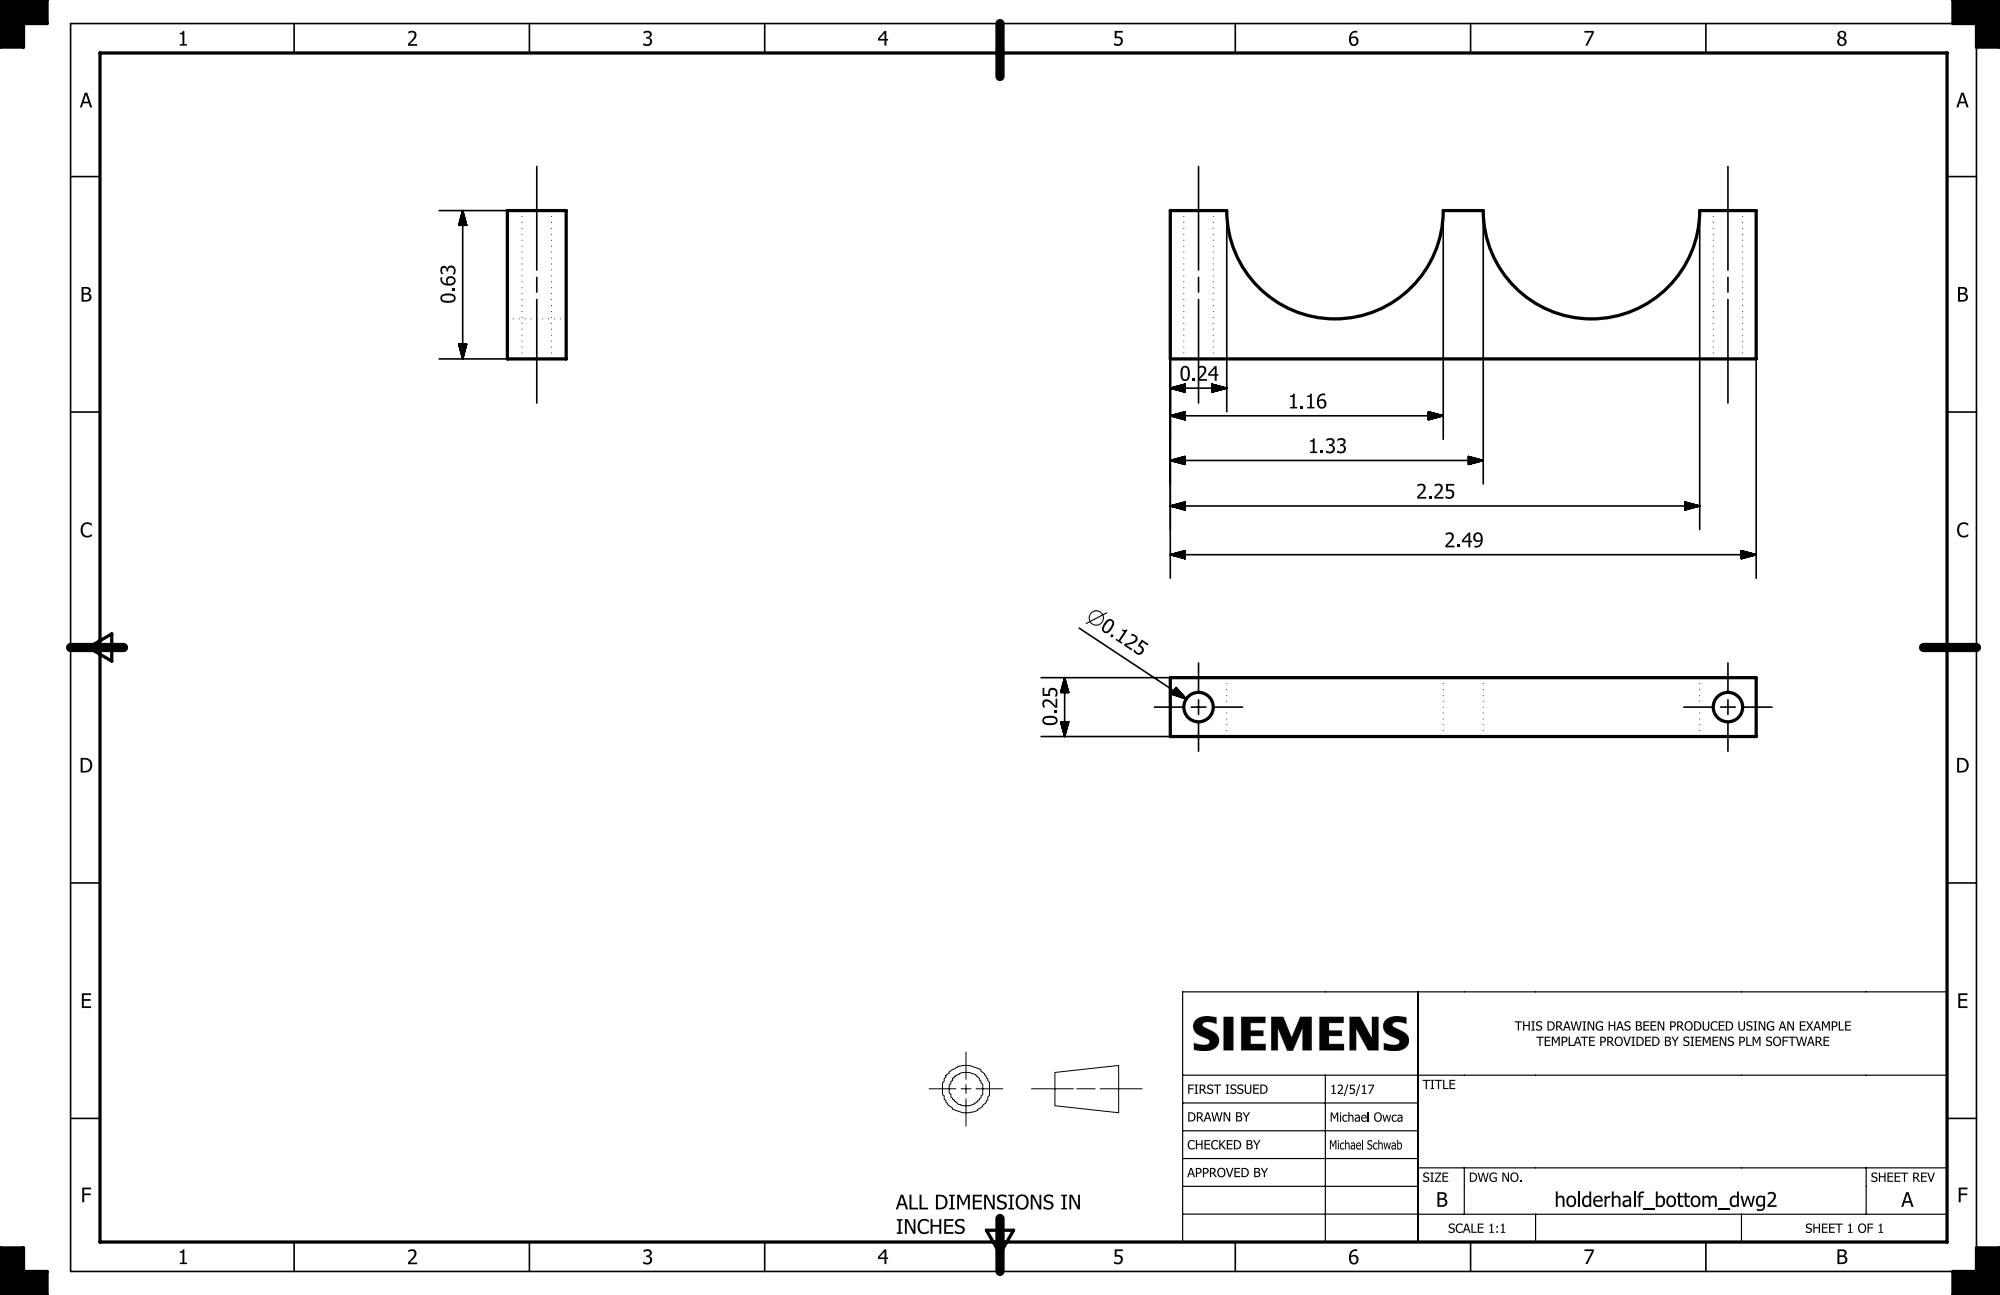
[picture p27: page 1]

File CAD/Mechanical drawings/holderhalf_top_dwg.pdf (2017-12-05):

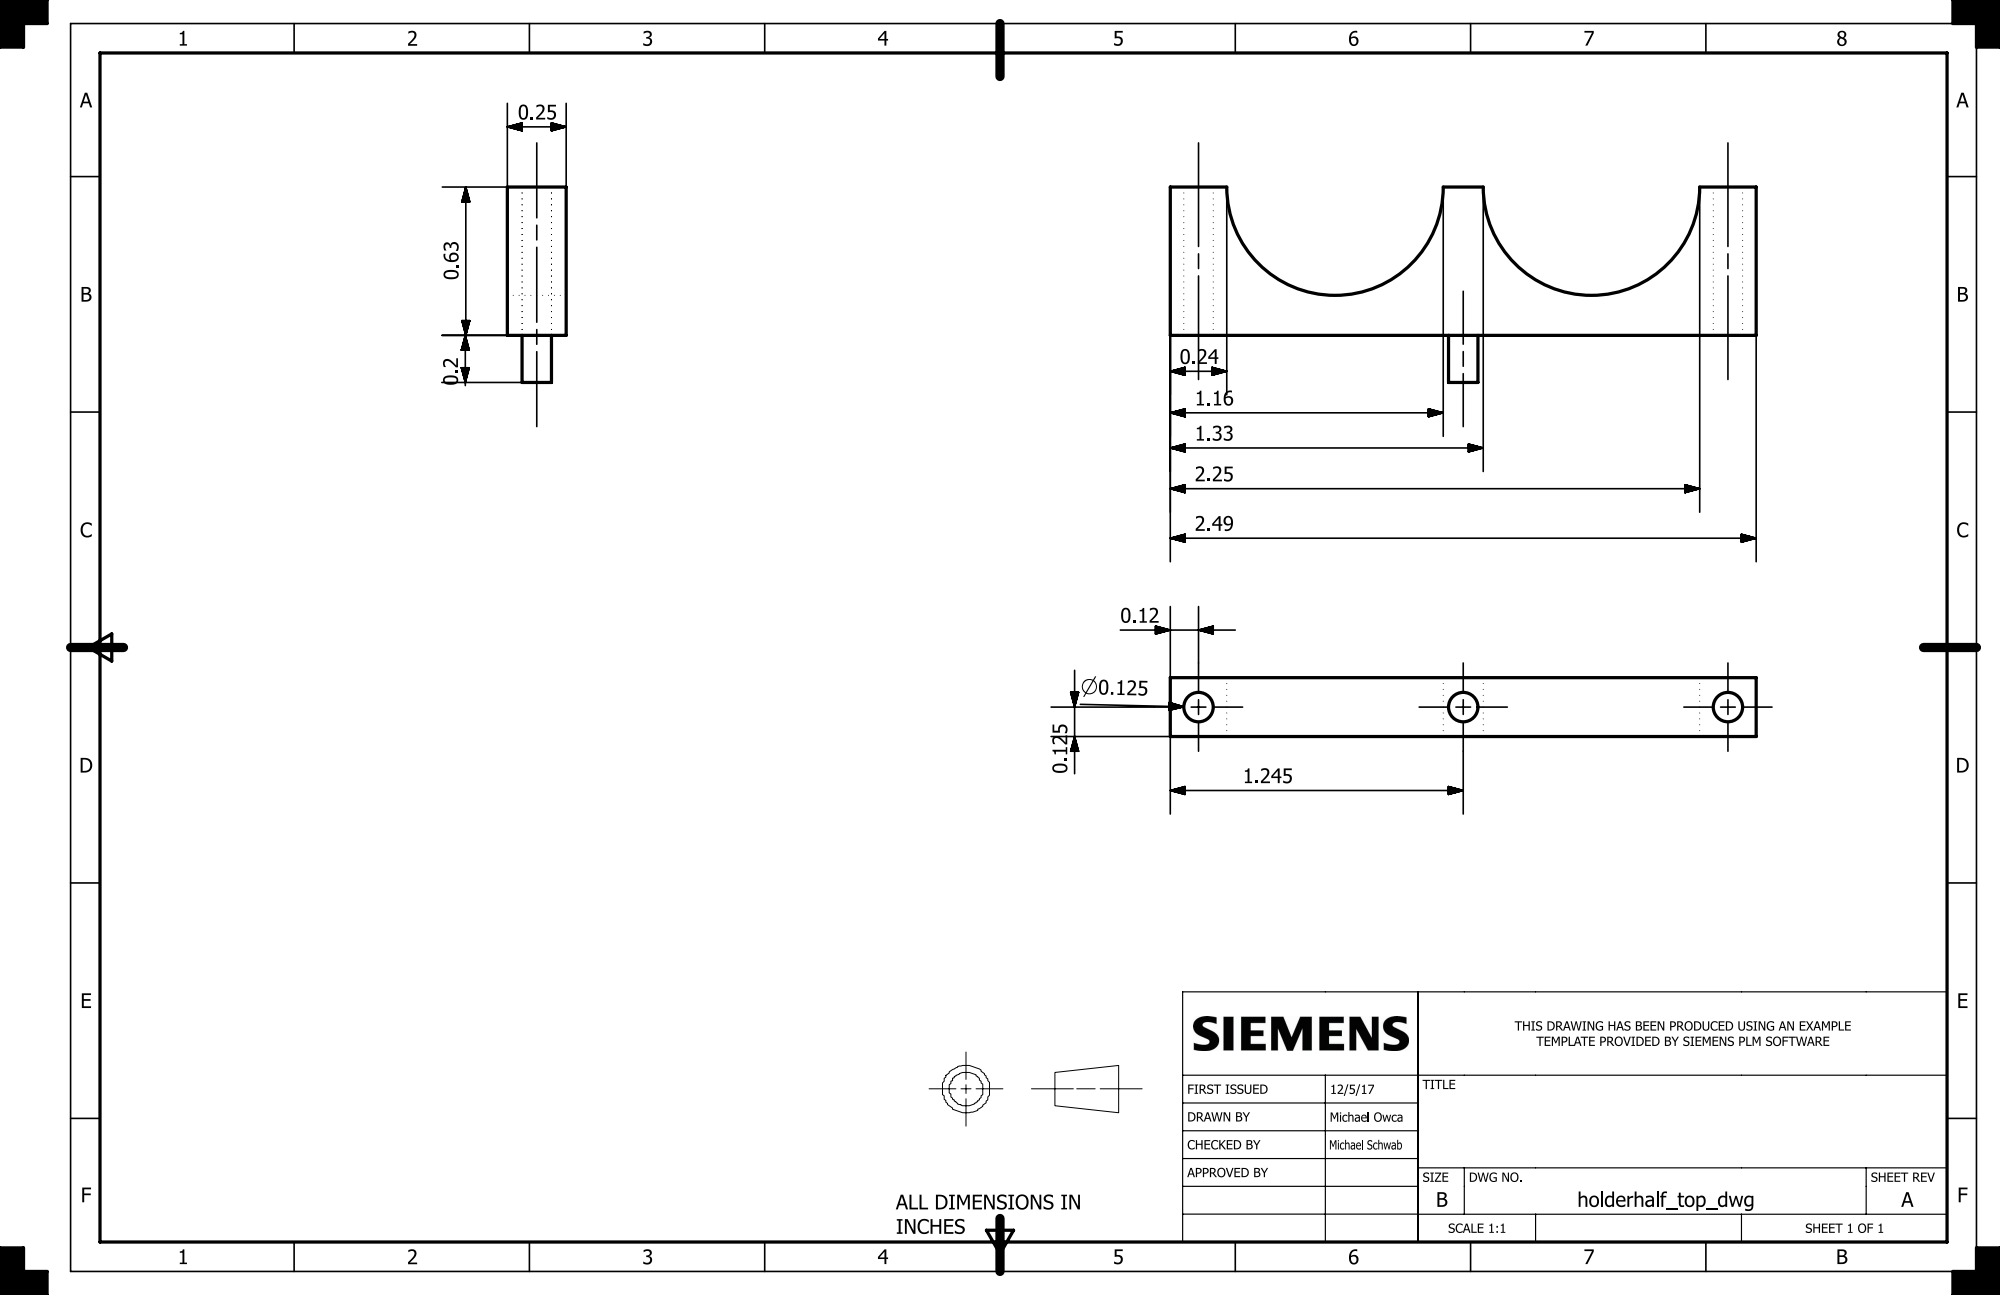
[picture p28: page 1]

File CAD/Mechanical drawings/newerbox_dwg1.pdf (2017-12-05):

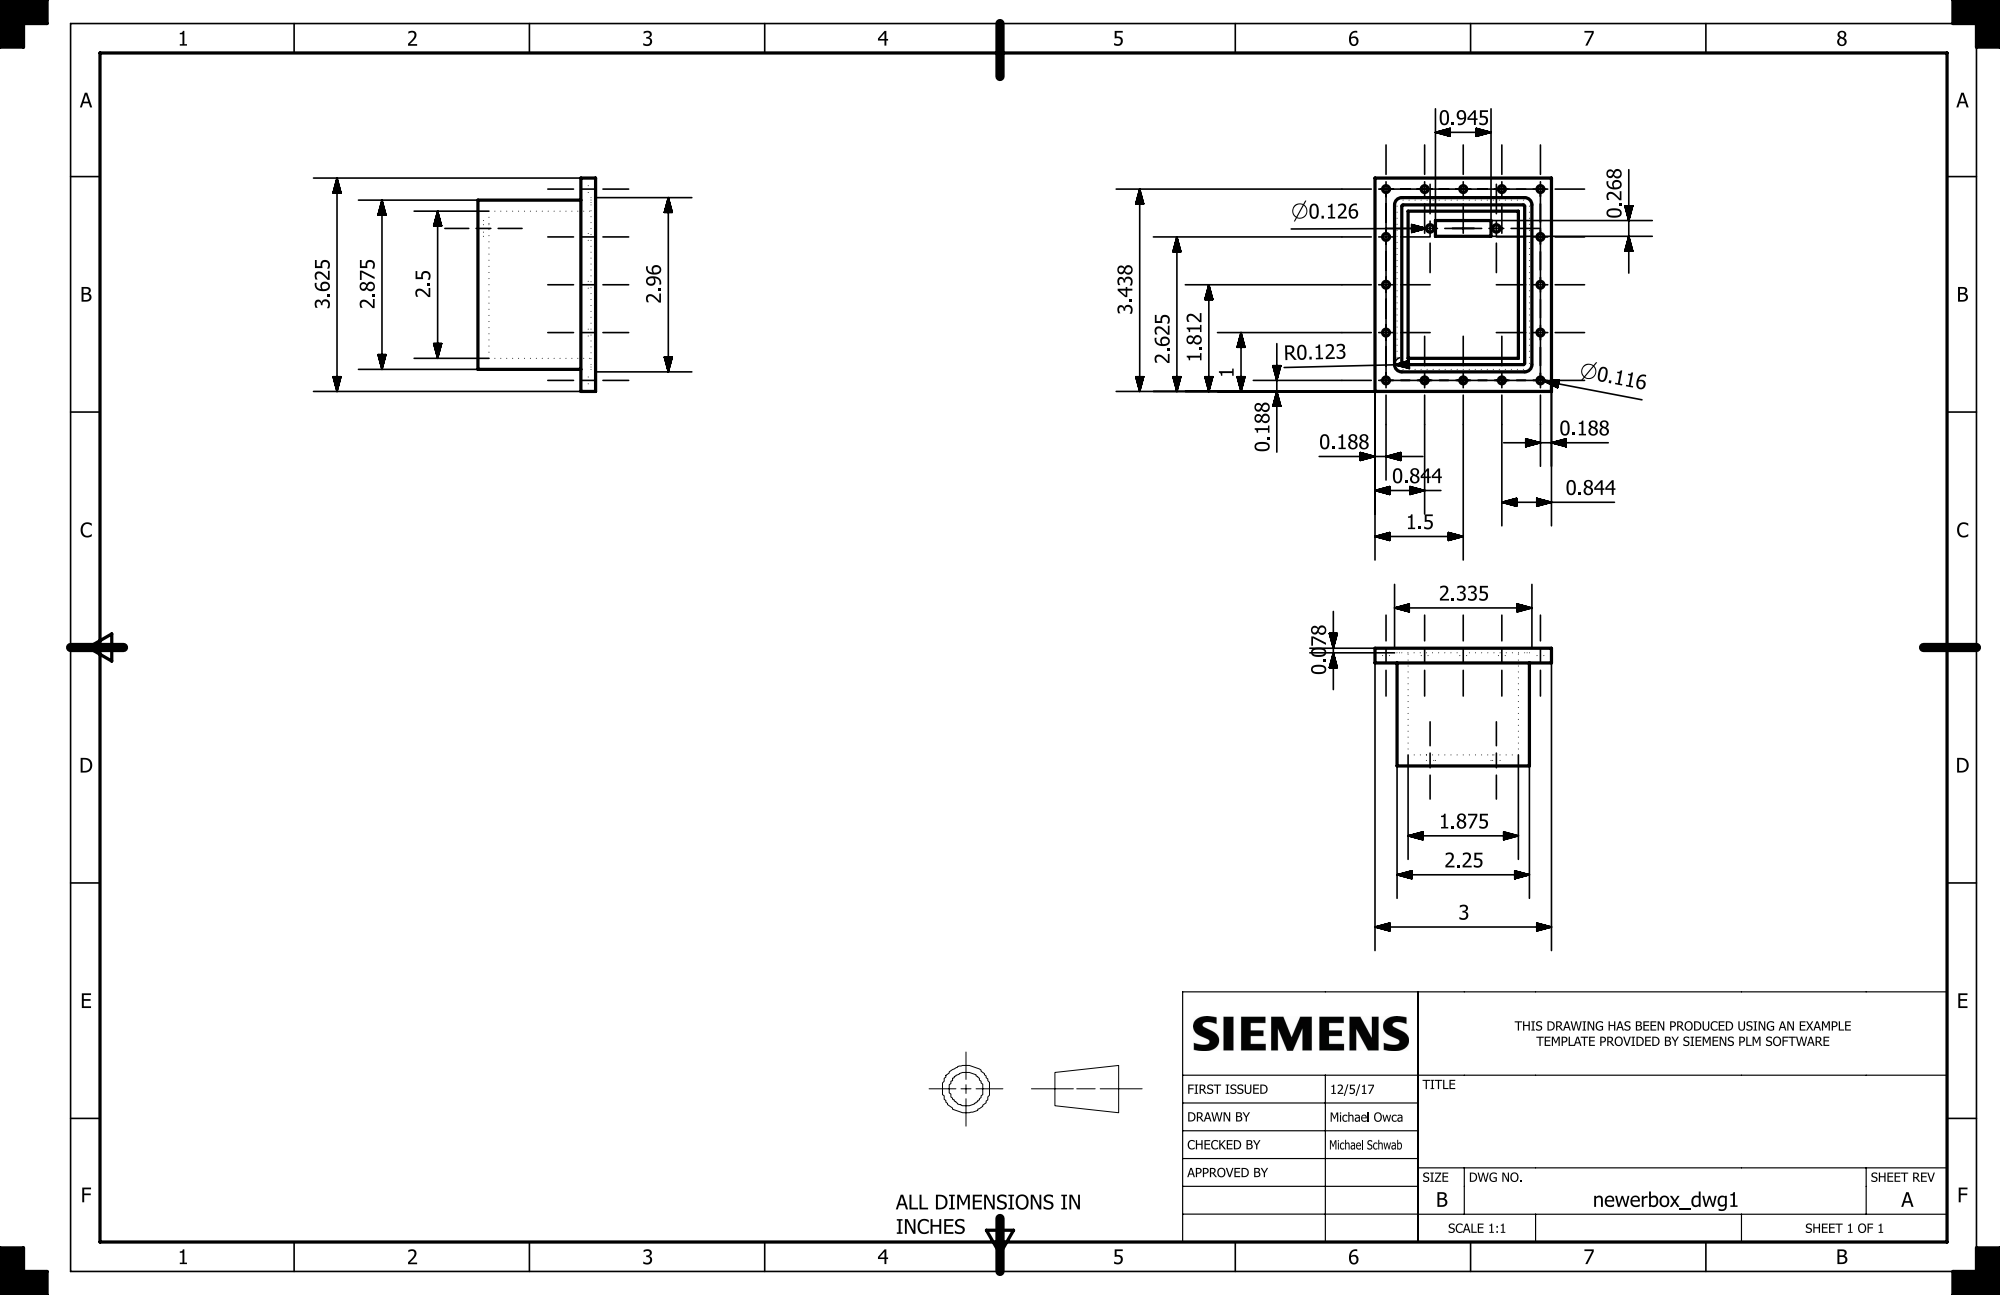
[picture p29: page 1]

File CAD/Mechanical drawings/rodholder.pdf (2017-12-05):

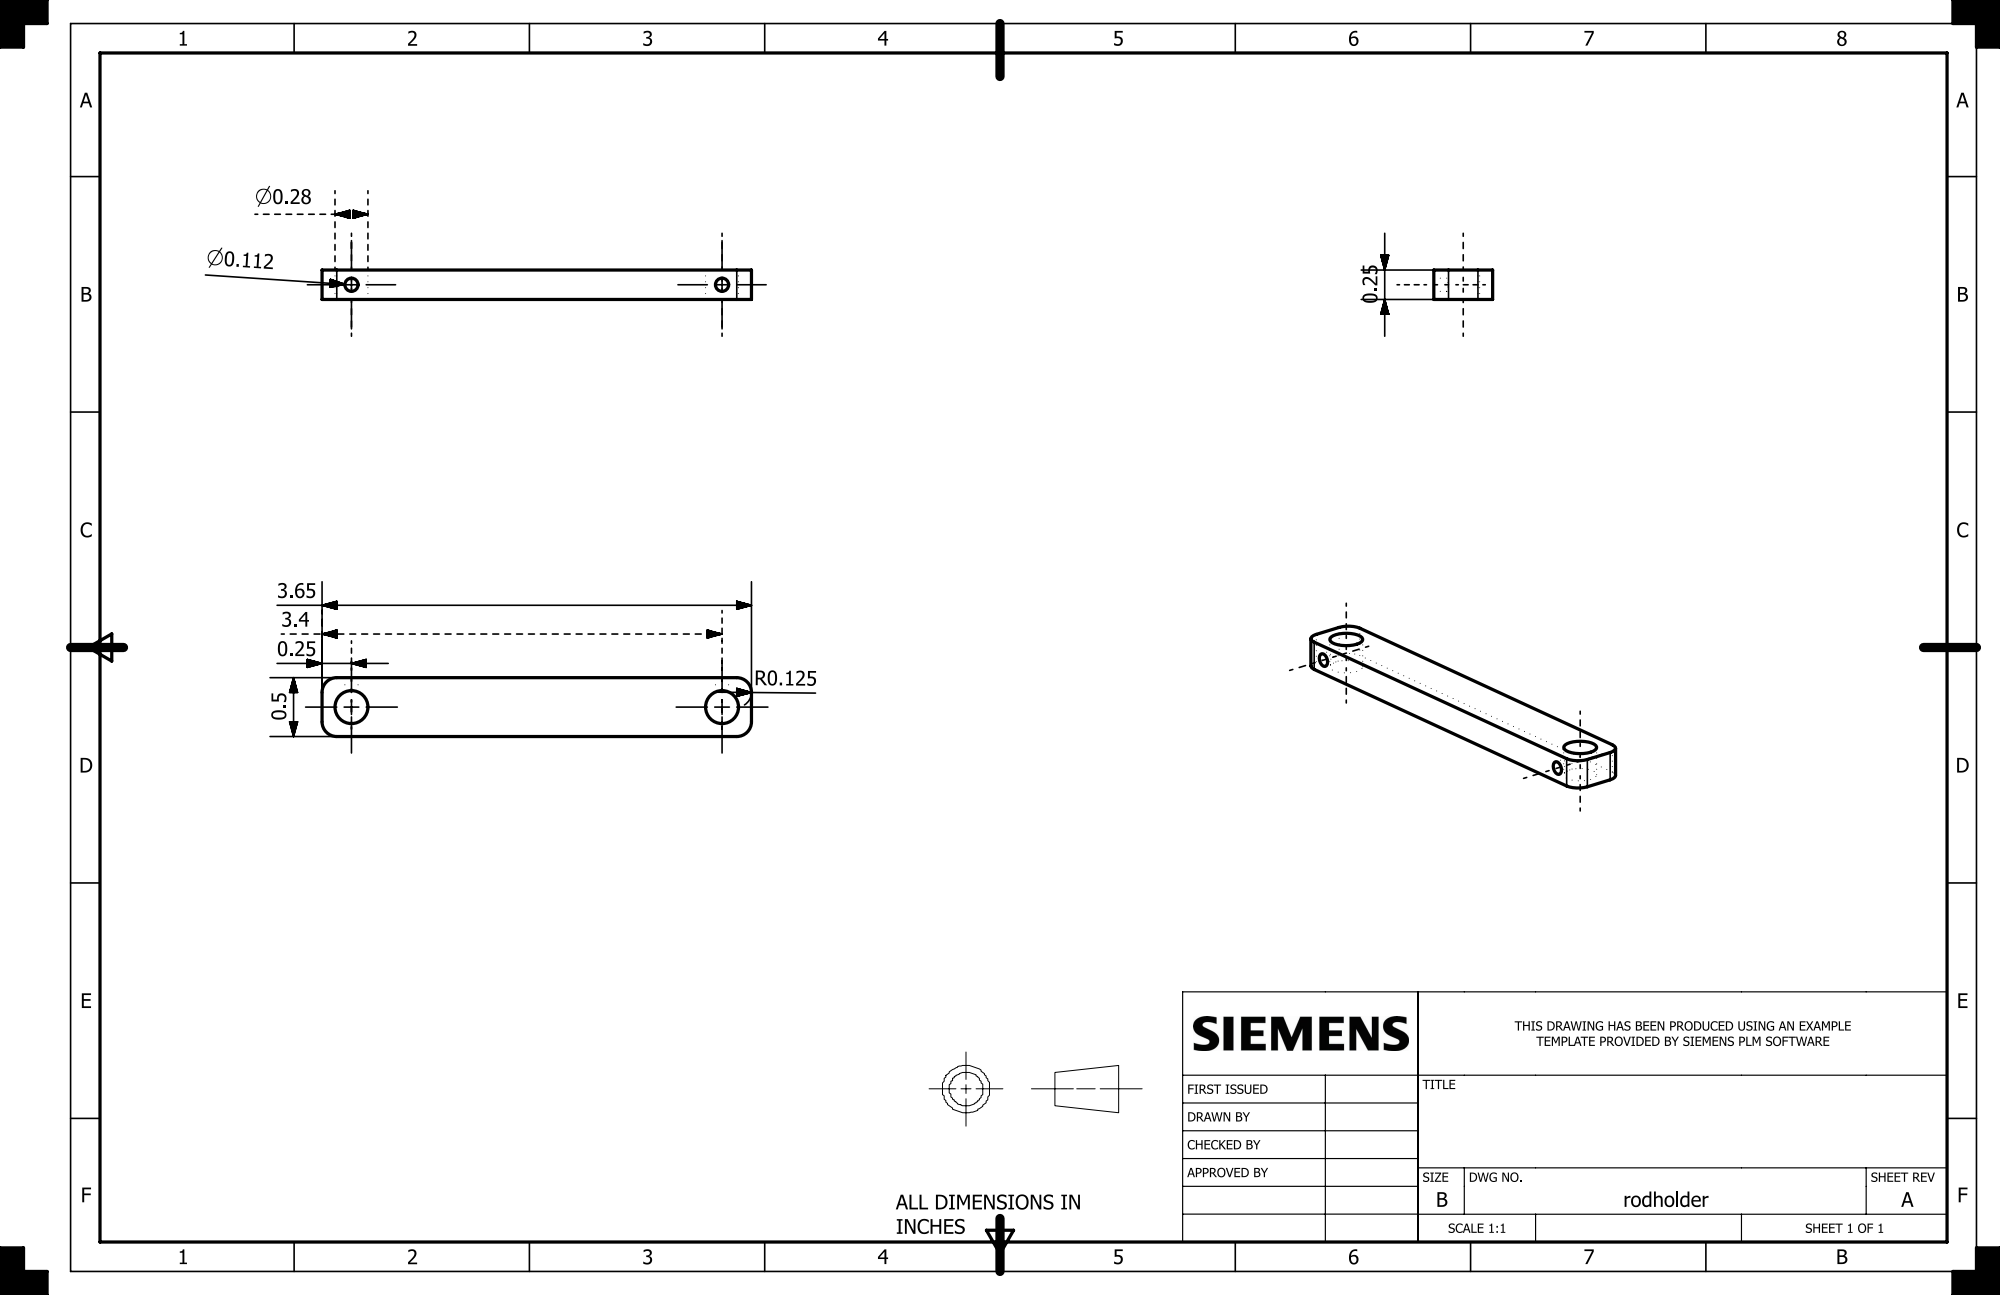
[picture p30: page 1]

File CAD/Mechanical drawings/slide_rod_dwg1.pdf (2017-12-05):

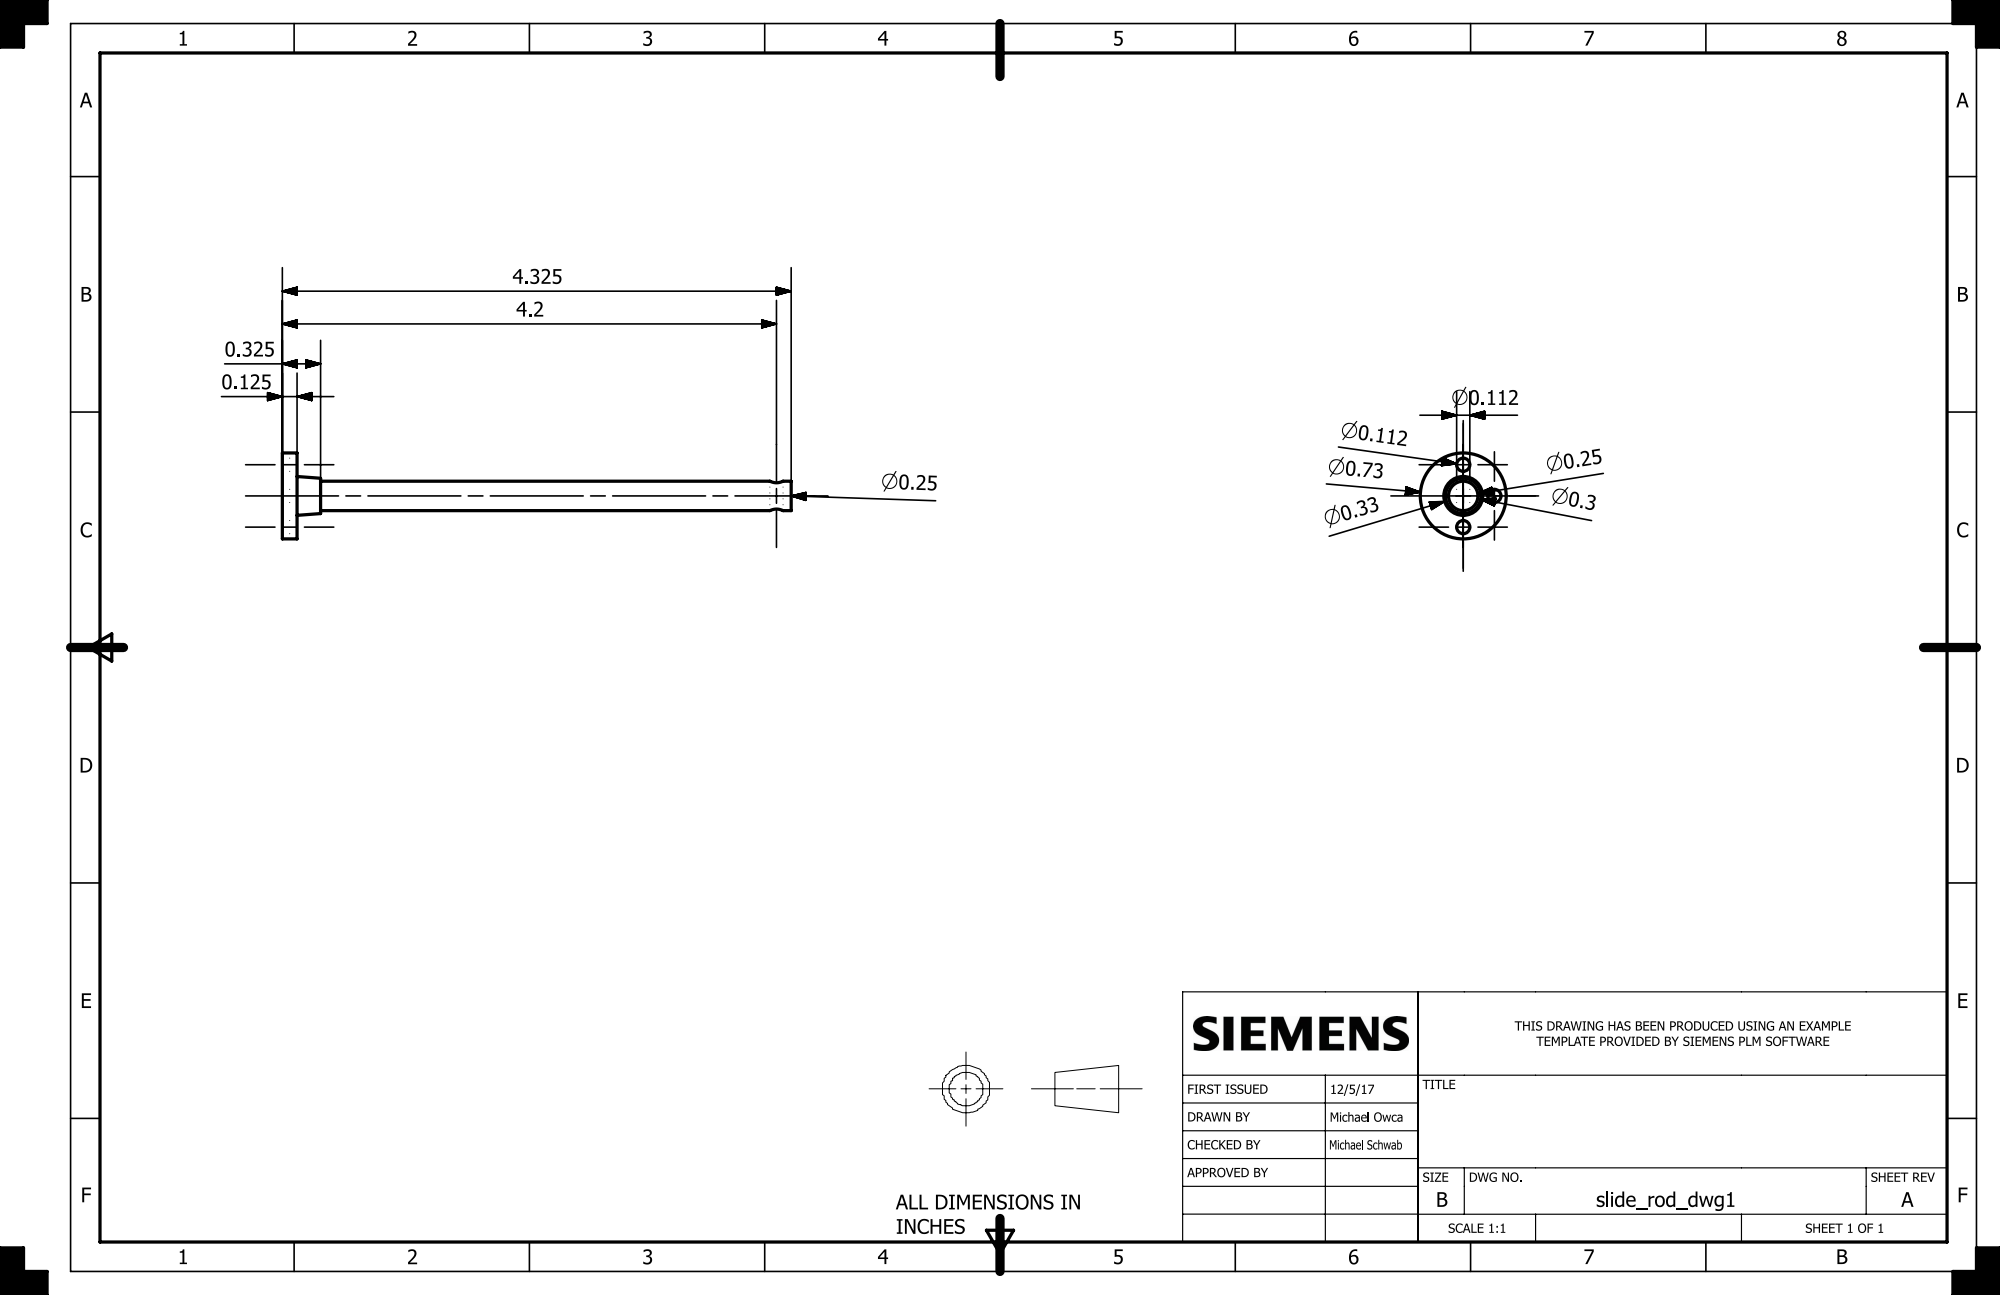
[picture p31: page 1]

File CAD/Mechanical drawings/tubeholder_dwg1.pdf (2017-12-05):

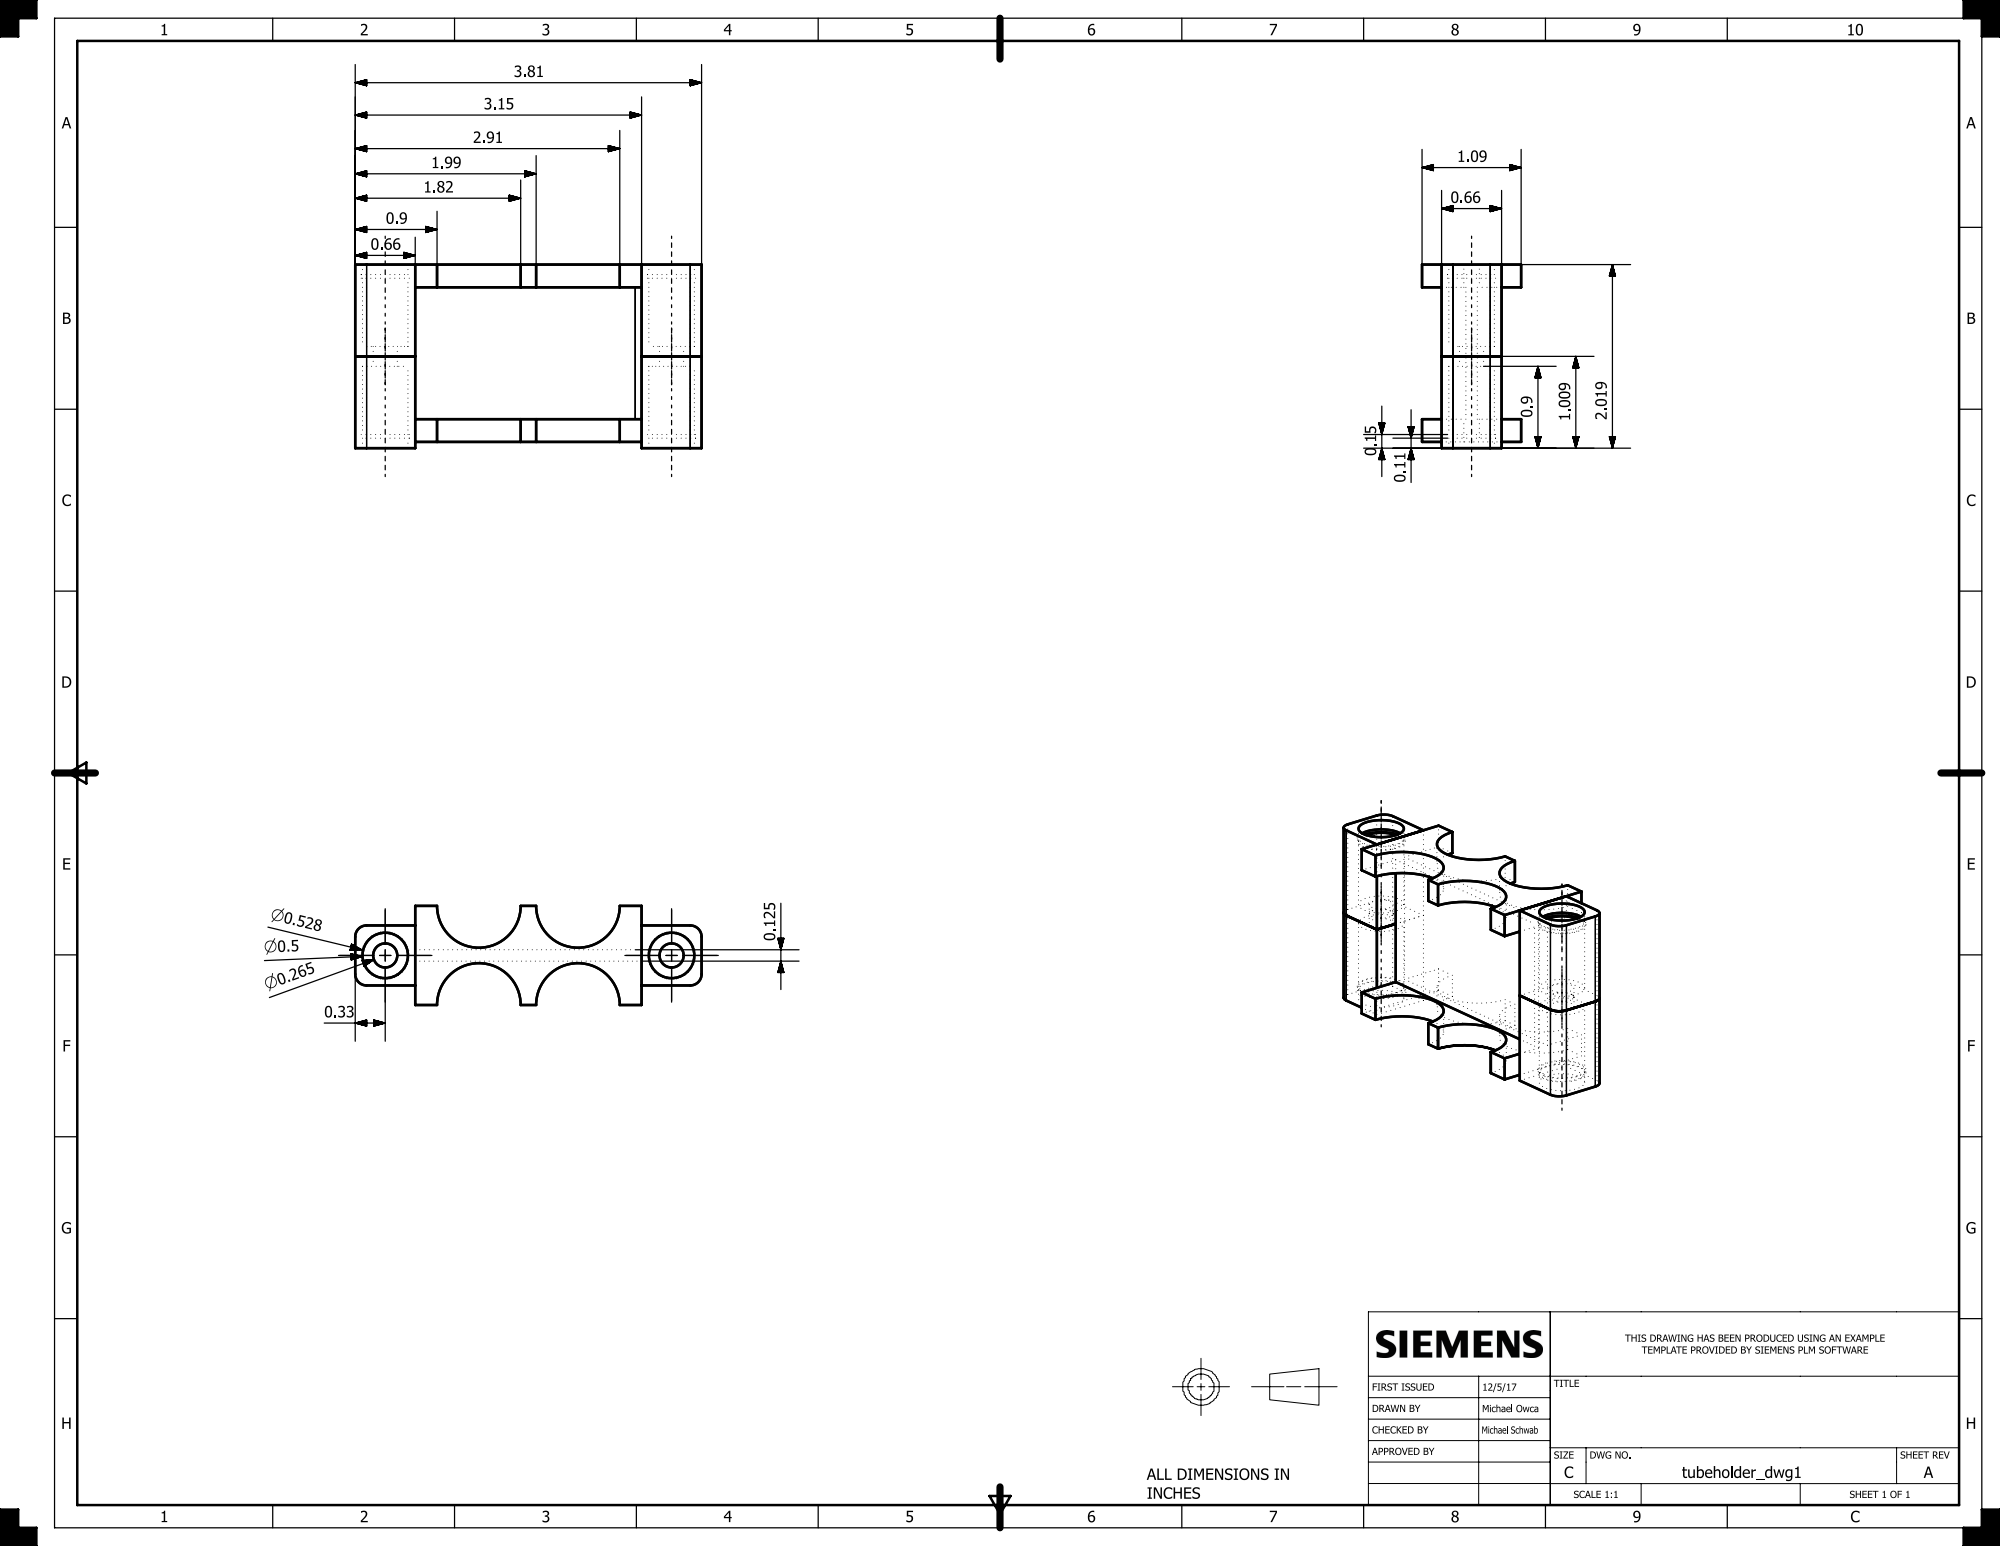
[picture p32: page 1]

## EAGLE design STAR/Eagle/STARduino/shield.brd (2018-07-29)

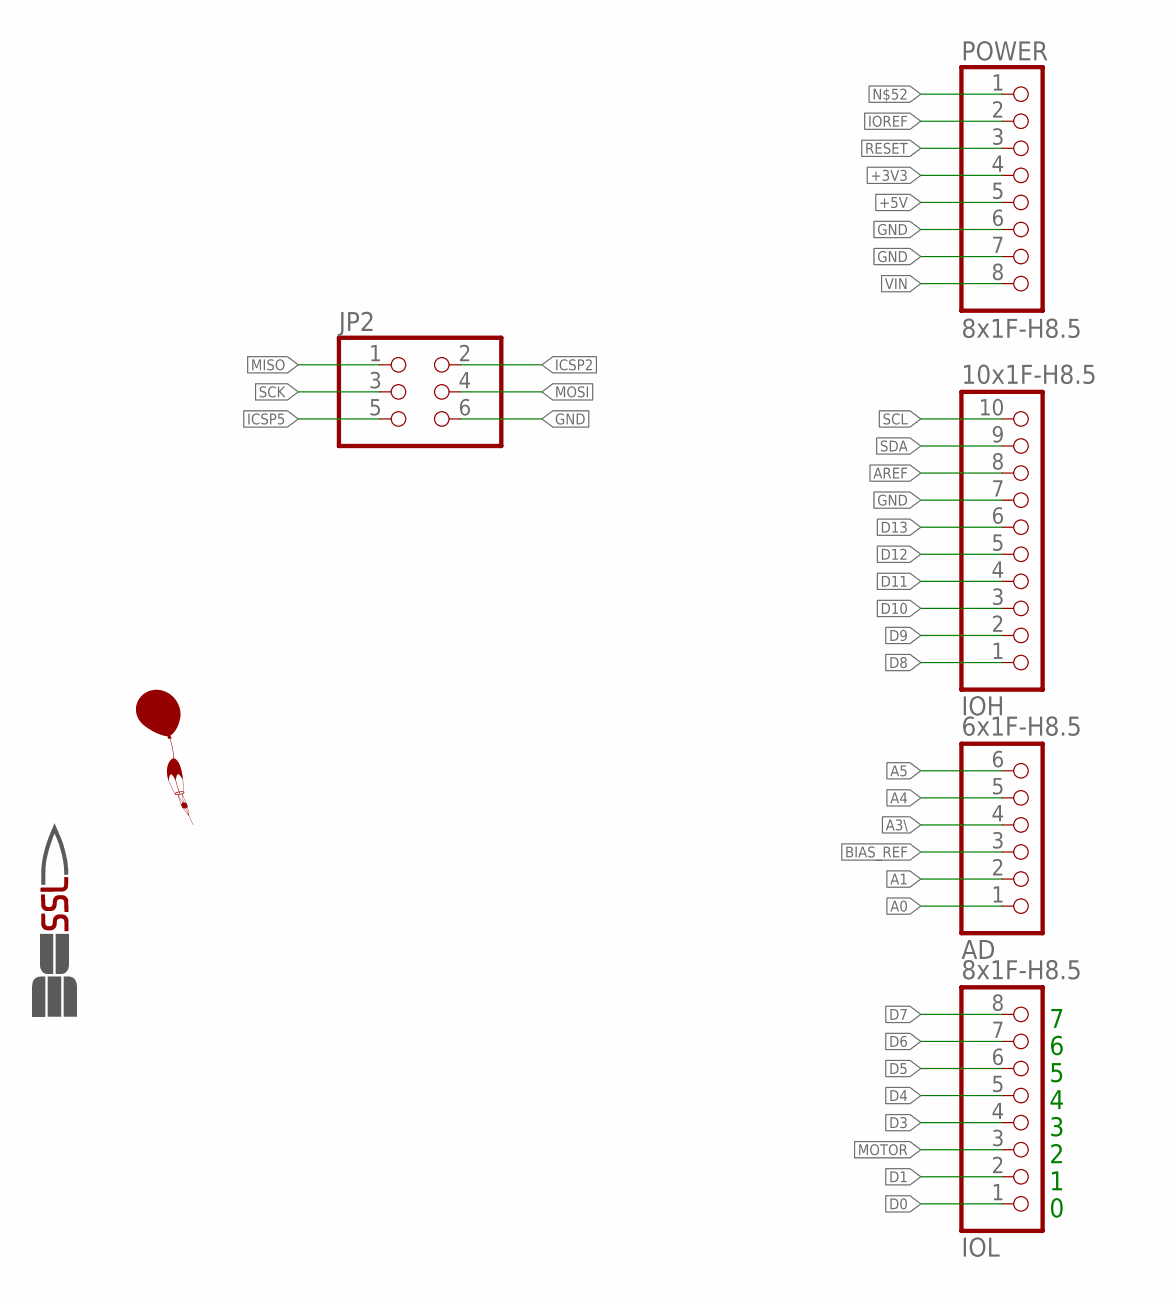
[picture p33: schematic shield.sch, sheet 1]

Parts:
AD: 6x1F-H8.5; 1X06
IOH: 10x1F-H8.5; 1X10
IOL: 8x1F-H8.5; 1X08
JP2: PINHD-2X3; 2X03
POWER: 8x1F-H8.5; 1X08
U$1: BALLOON
U$2: SSLORIG; SSL

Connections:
+3V3: POWER.4; also elsewhere on the board
+5V: POWER.5
A0: AD.1
A1: AD.2
A3\: AD.4
A4: AD.5
A5: AD.6
AREF: IOH.8
BIAS_REF: AD.3; also elsewhere on the board
D0: IOL.1
D1: IOL.2
D3: IOL.4
D4: IOL.5
D5: IOL.6
D6: IOL.7
D7: IOL.8
D8: IOH.1
D9: IOH.2
D10: IOH.3
D11: IOH.4
D12: IOH.5
D13: IOH.6
GND: IOH.7, JP2.6, POWER.6, POWER.7; also elsewhere on the board
ICSP2: JP2.2
ICSP5: JP2.5
IOREF: POWER.2
MISO: JP2.1; also elsewhere on the board
MOSI: JP2.4; also elsewhere on the board
MOTOR: IOL.3; also elsewhere on the board
RESET: POWER.3
SCK: JP2.3; also elsewhere on the board
SCL: IOH.10; also elsewhere on the board
SDA: IOH.9; also elsewhere on the board
VIN: POWER.8

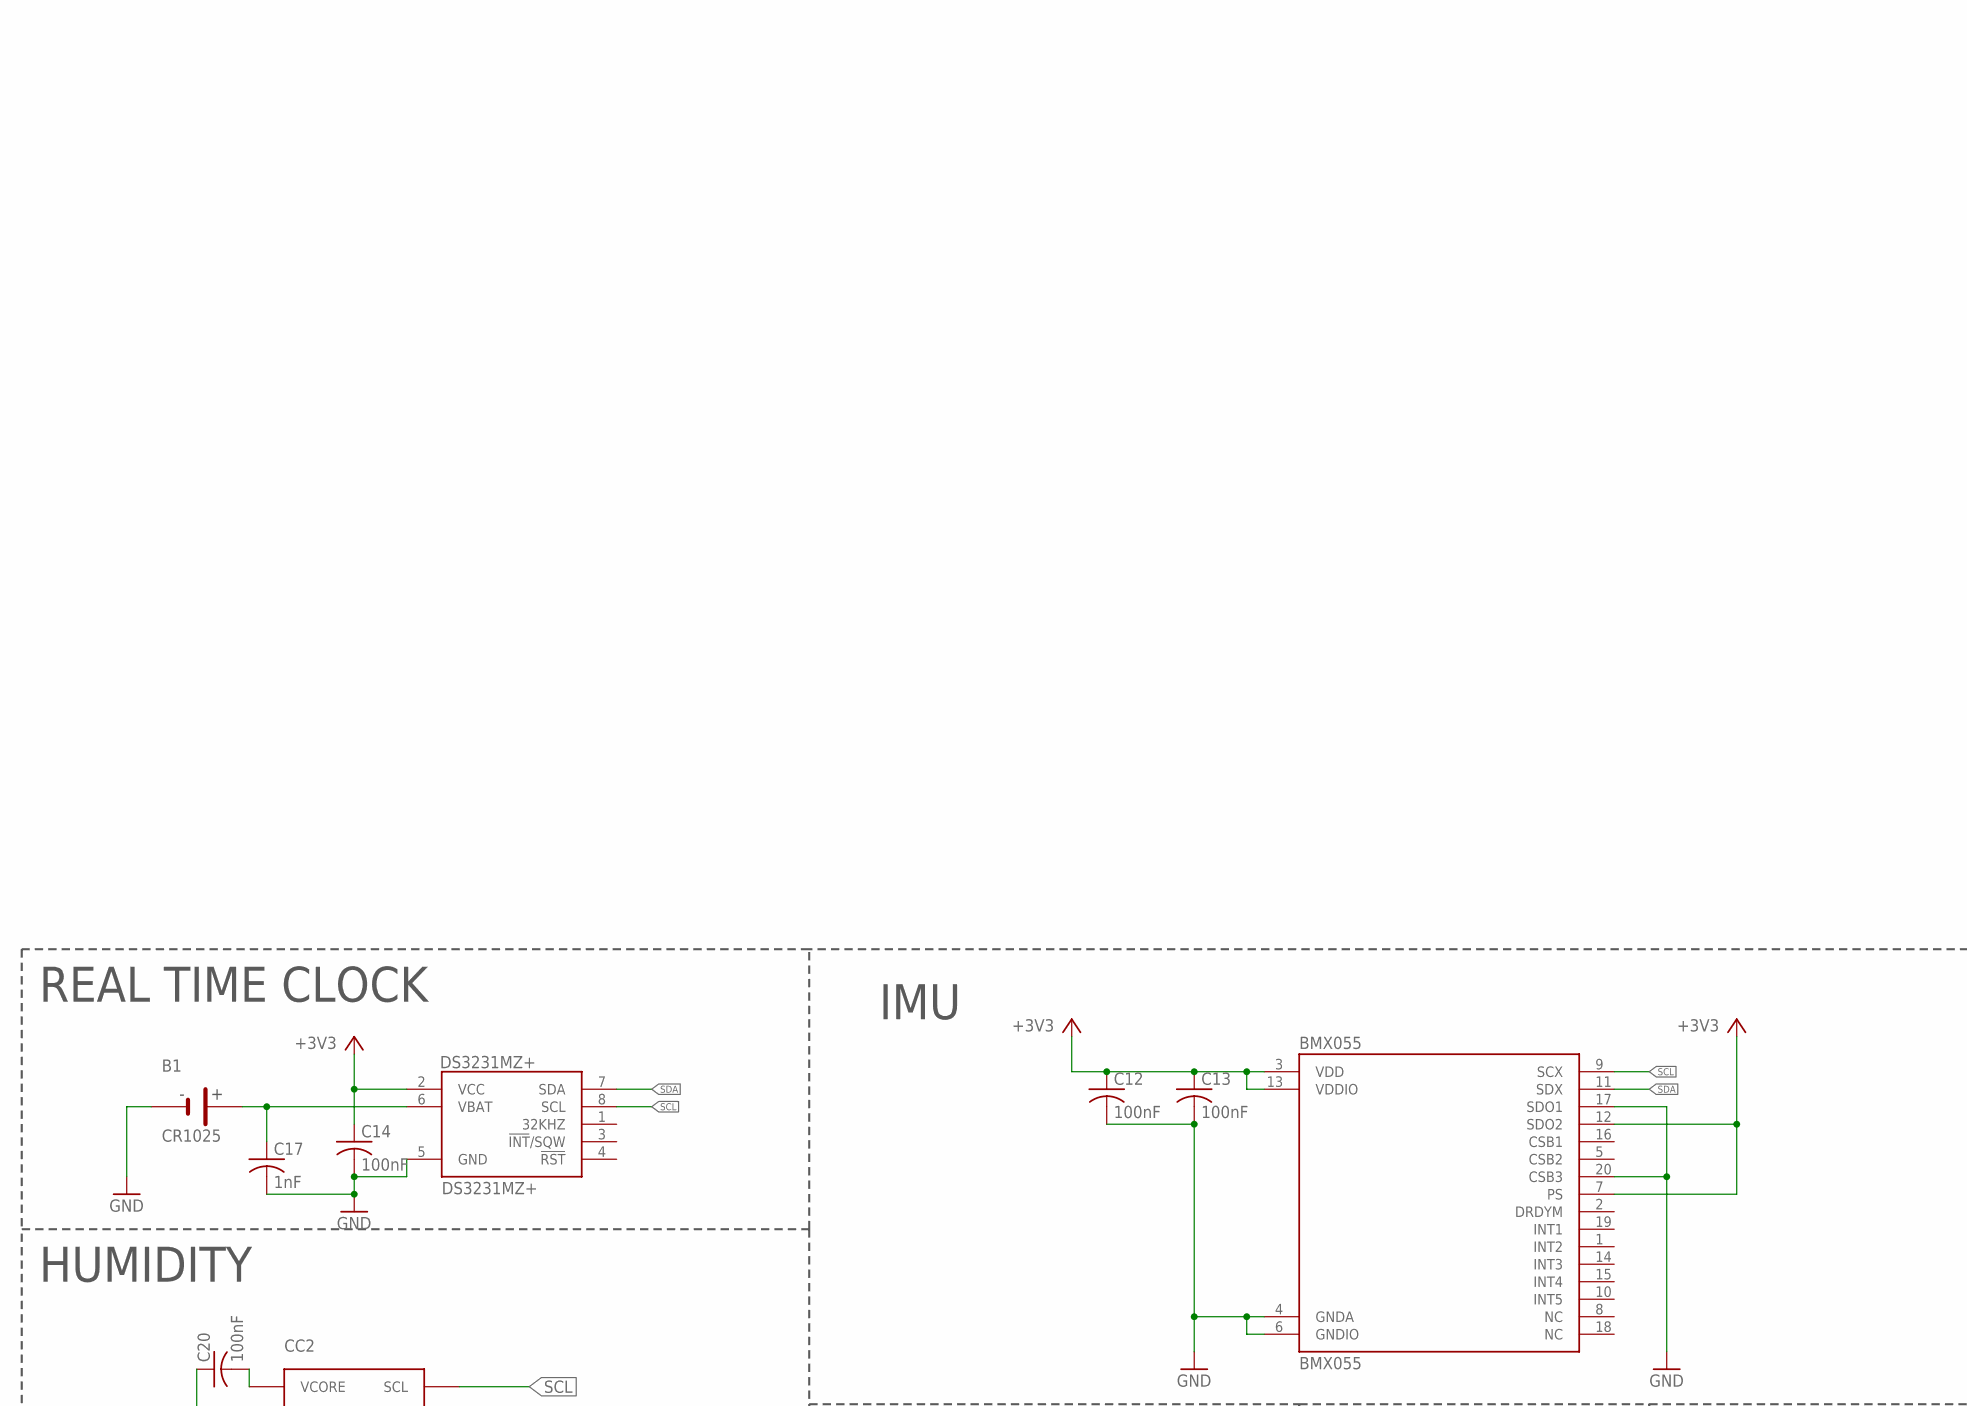
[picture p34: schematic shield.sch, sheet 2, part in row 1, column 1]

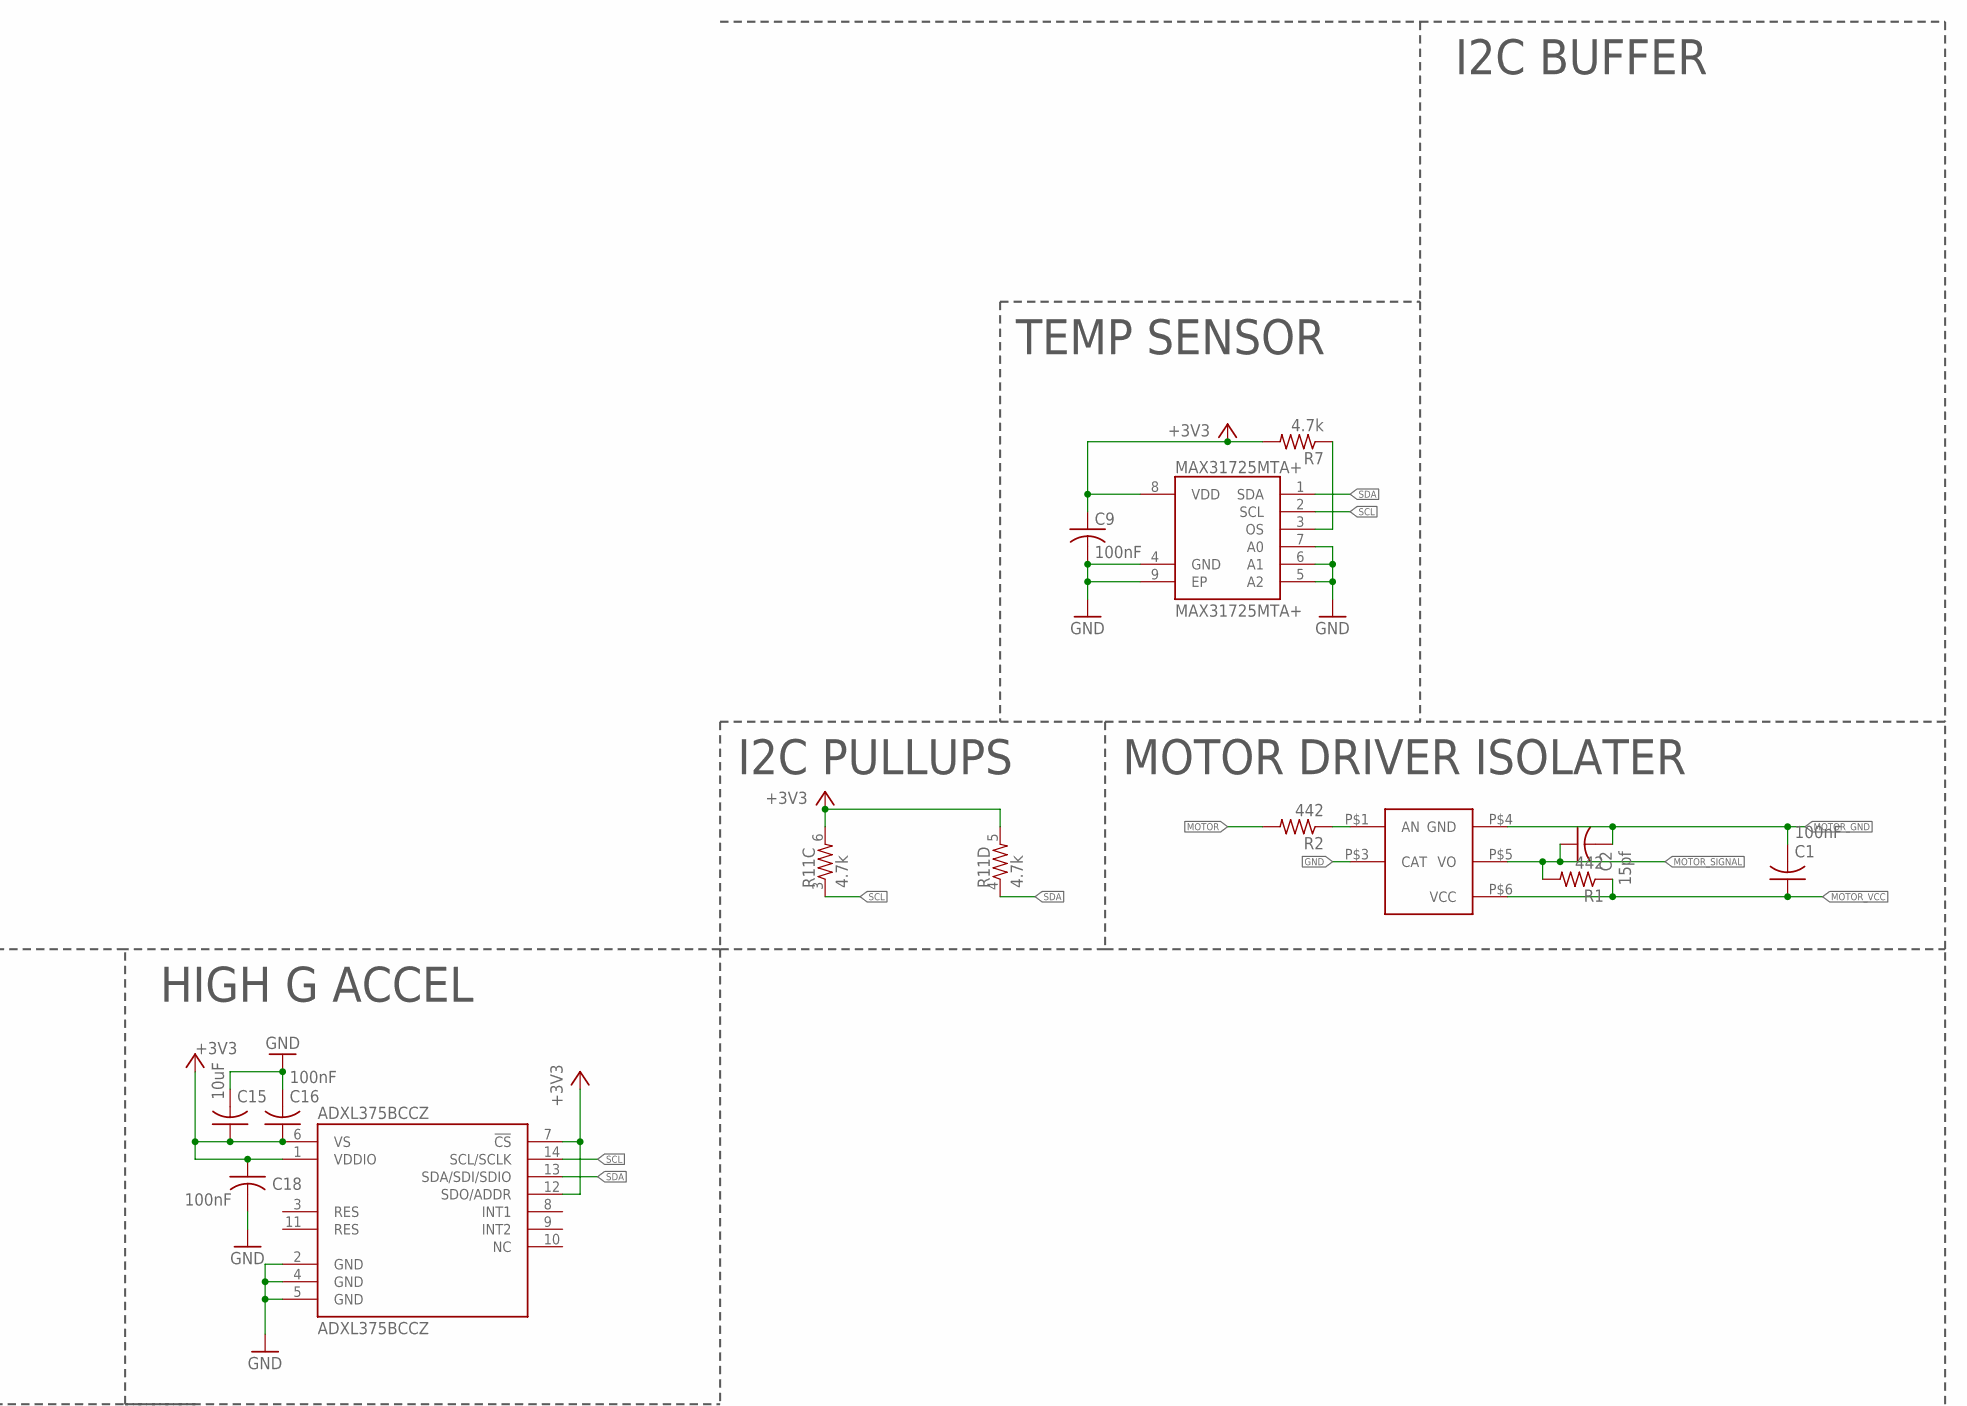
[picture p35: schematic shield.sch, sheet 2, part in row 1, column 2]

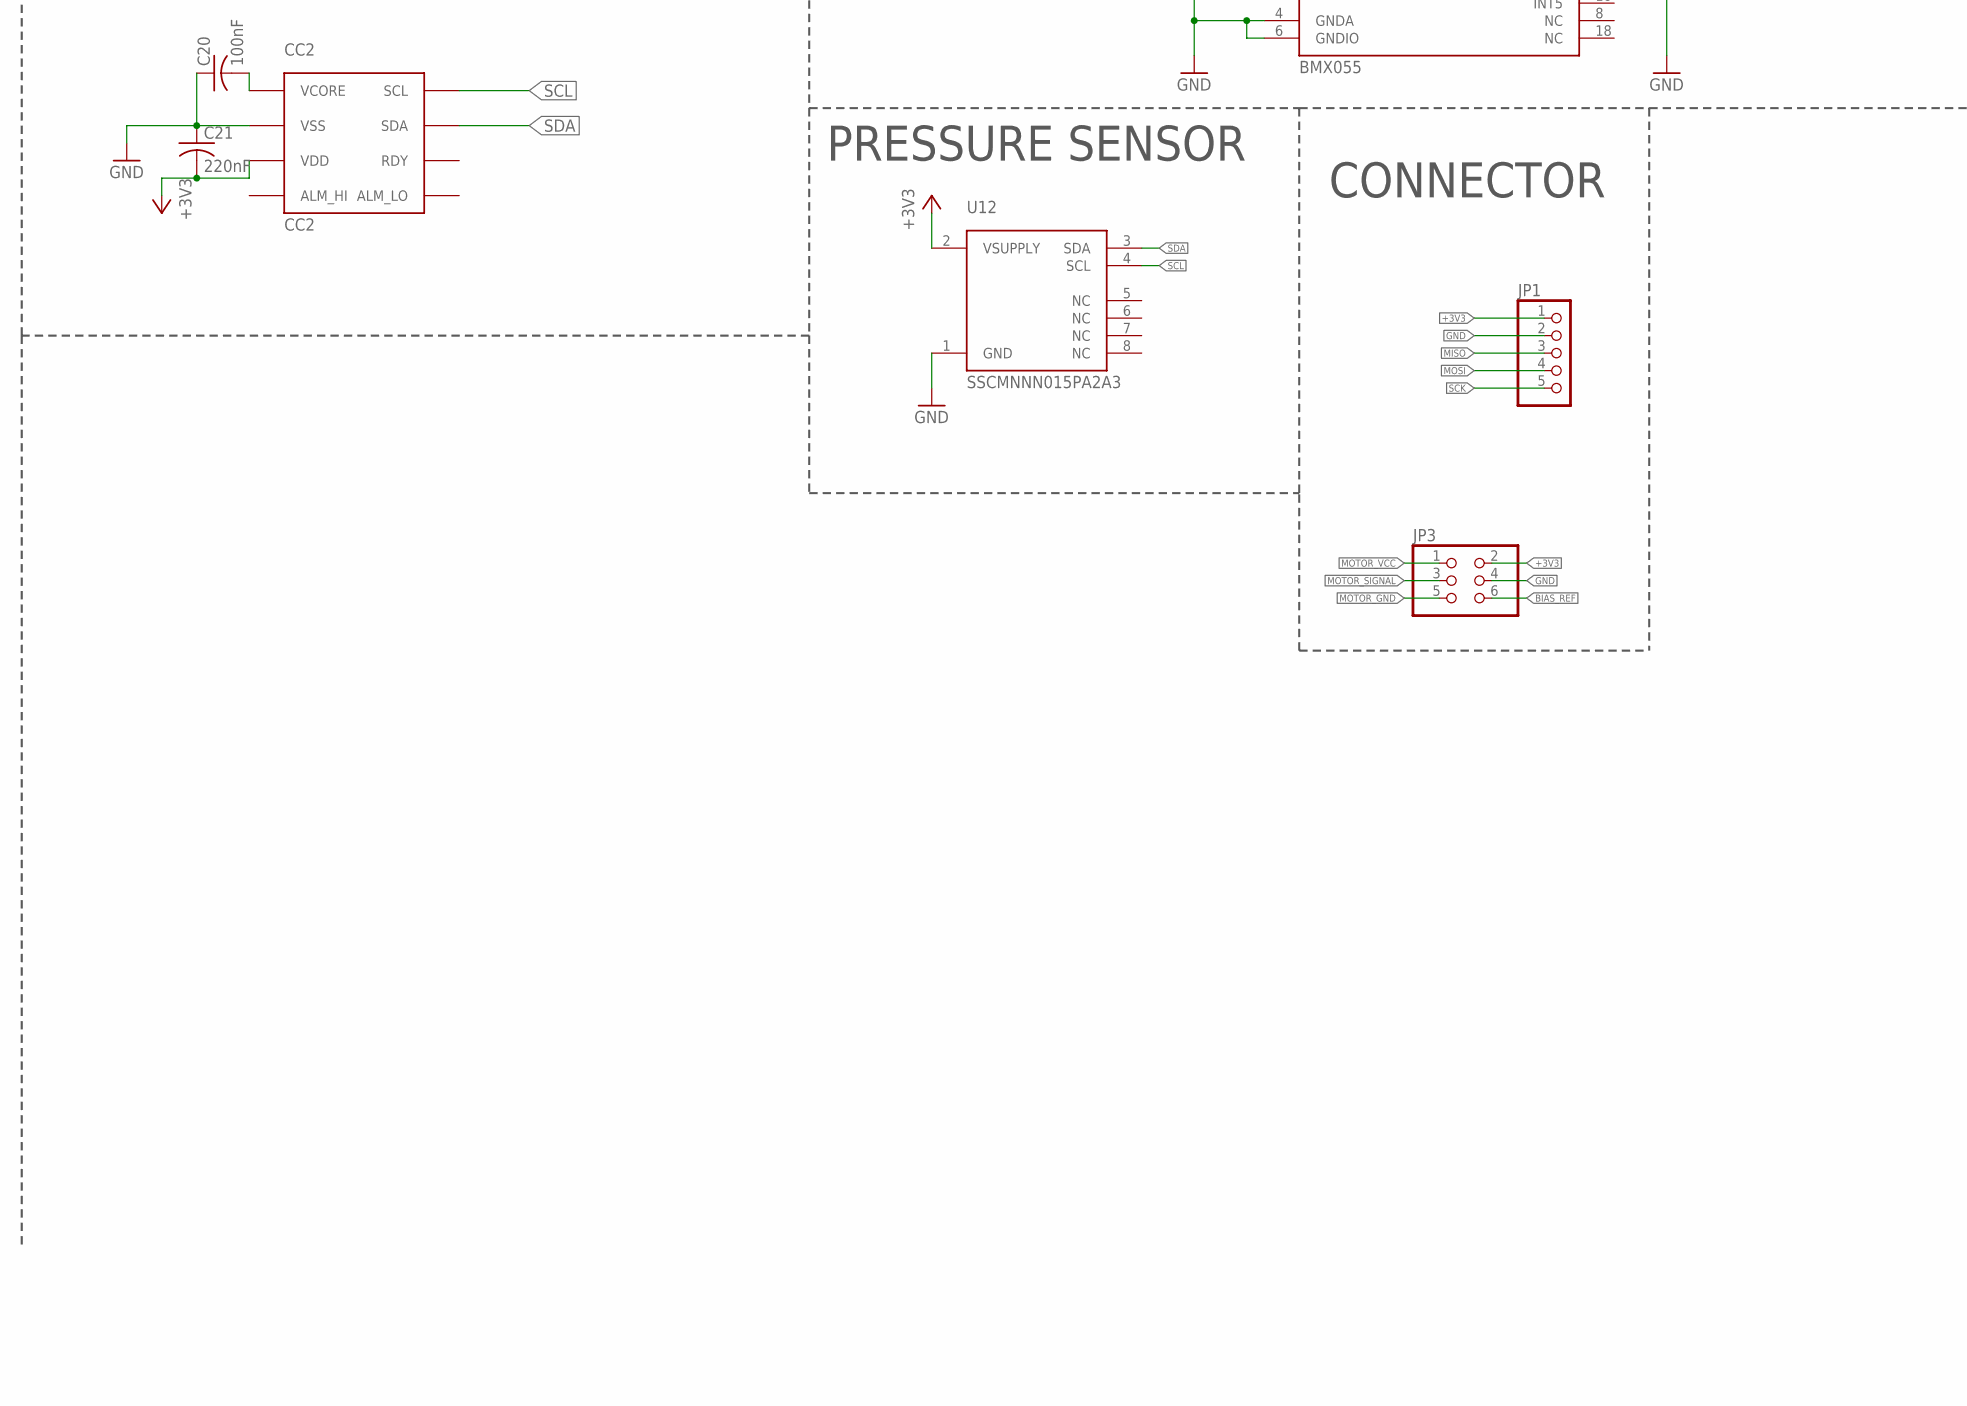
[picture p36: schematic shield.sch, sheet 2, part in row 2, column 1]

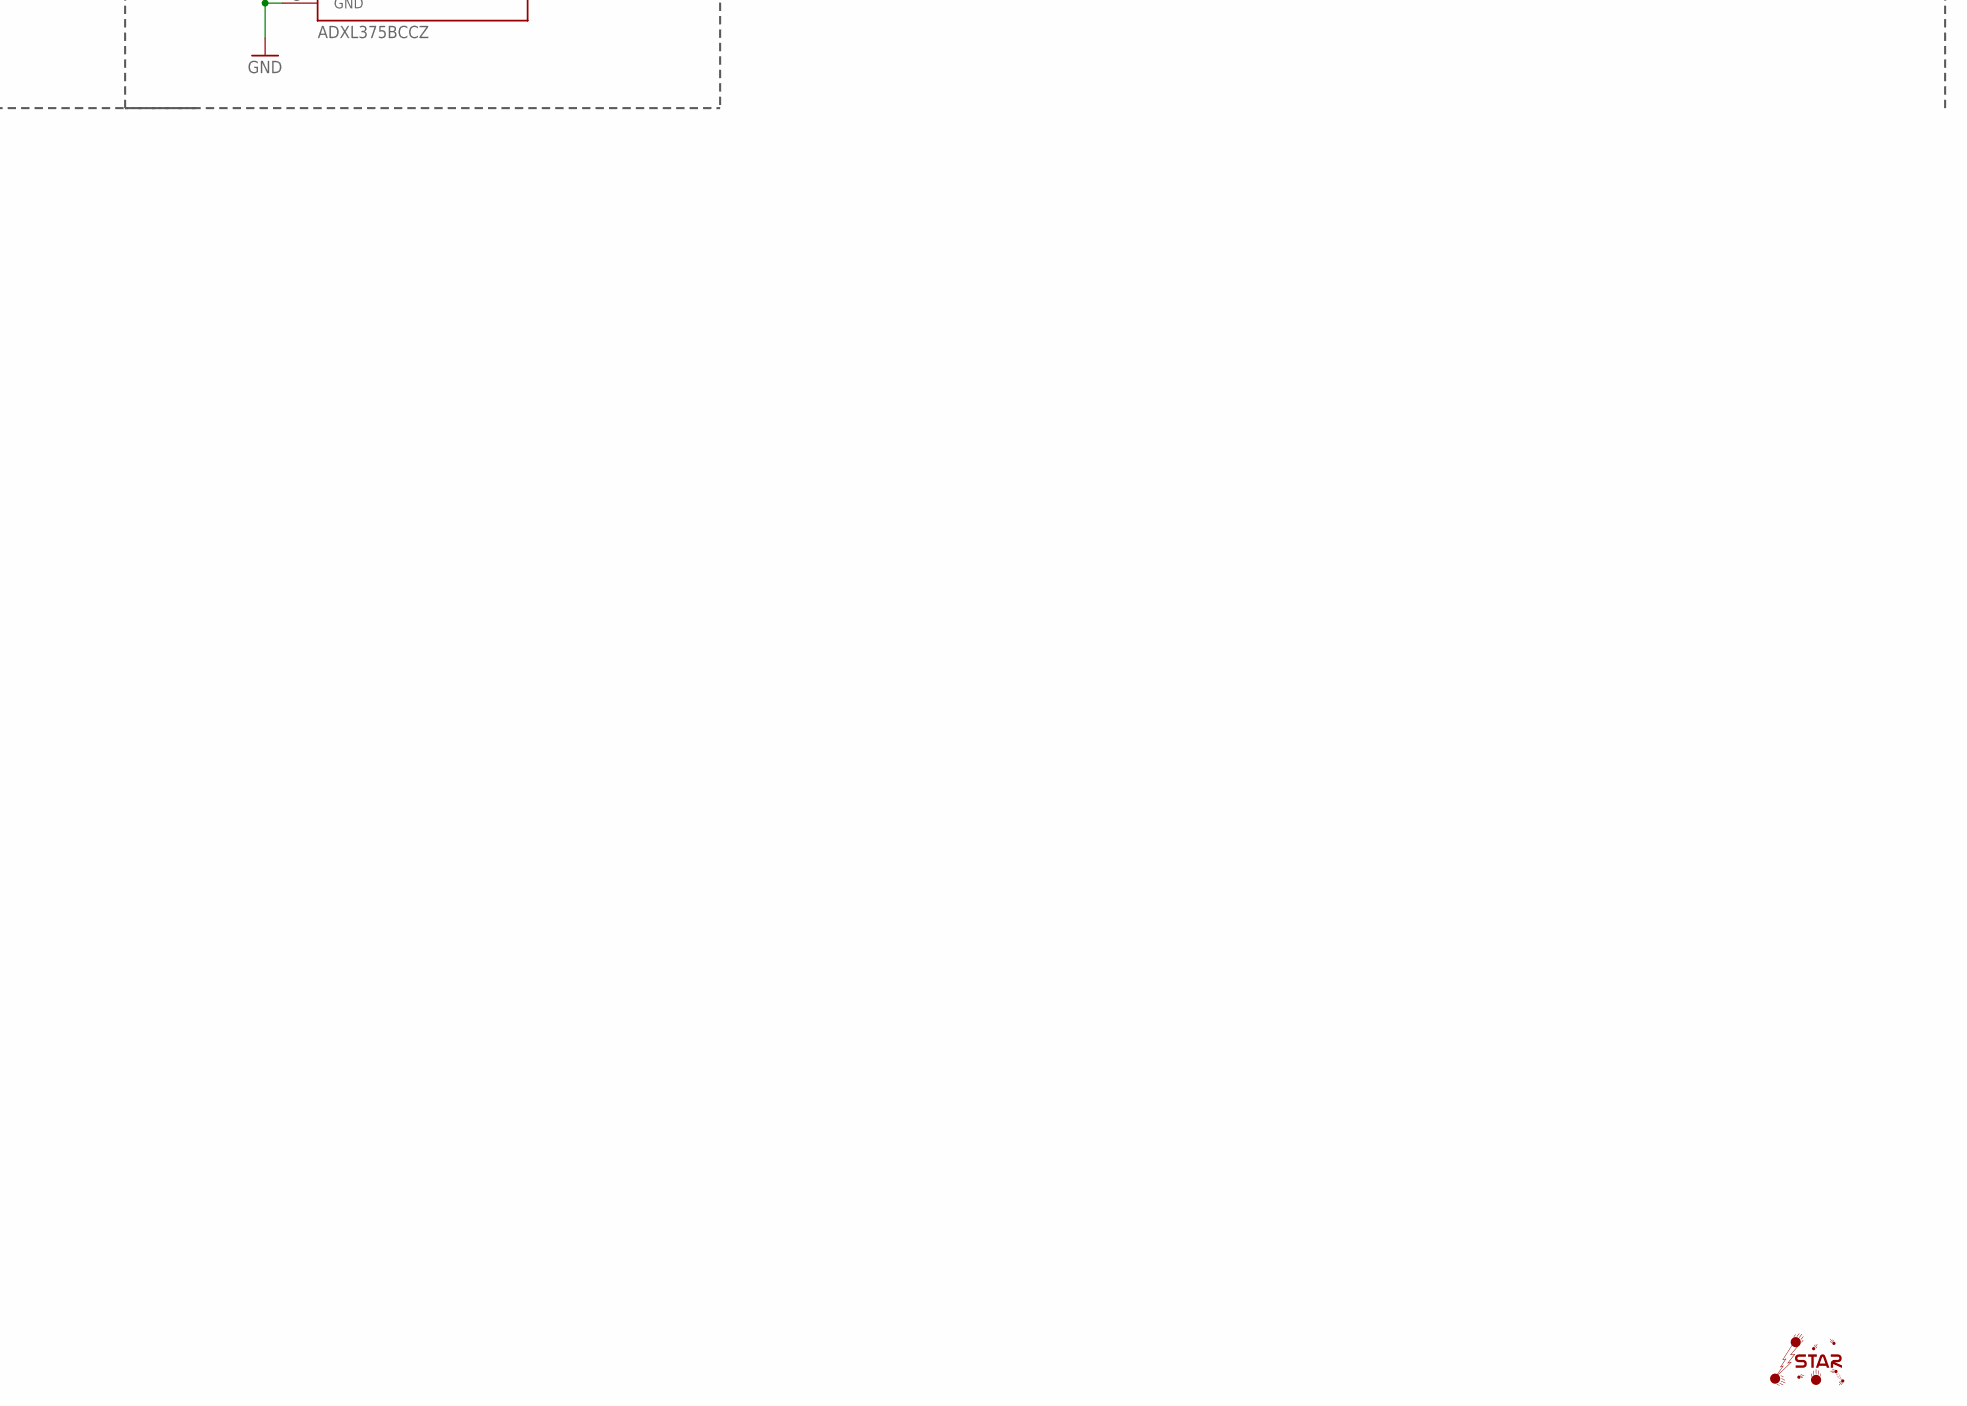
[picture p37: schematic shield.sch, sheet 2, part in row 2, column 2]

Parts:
ADXL375BCCZ: ADXL375BCCZ; LGA-14
B1: CR1025
BMX055: BMX055; LGA-20
C1, C9, C12, C13, C14, C16, C18, C20: 100nF; C0603
C2: 15pf; C0603
C15: 10uF; C0603
C17: 1nF; C0603
C21: 220nF; C0603
CC2: CC2
DS3231MZ+: DS3231MZ+; SOIC-8
IMAG2: STAR; STAR_.3IN
JP1: PINHD-1X5; 1X05
JP3: PINHD-2X3; 2X03
MAX31725MTA+: MAX31725MTA+; DFN-8
MOTORDRIVER: FODM8061-D; SO5
R1, R2: 442; R0805
R7: 4.7k; R0603
R11: 4.7k; 0603-ARV
U12: SSCMNNN015PA2A3; HSC-SMT-8

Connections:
+3V3: ADXL375BCCZ.1 (VDDIO), ADXL375BCCZ.6 (VS), ADXL375BCCZ.7 (!CS!), ADXL375BCCZ.12 (SDO/ADDR), BMX055.3 (VDD), BMX055.7 (PS), BMX055.12 (SDO2), BMX055.13 (VDDIO), C9.1, C12.1, C13.1, C14.1, C15.1, C16.1, C18.1, C21.2, CC2.P$7 (VDD), DS3231MZ+.2 (VCC), JP1.1, JP3.2, MAX31725MTA+.8 (VDD), R7.2, R11.5 (2), R11.6 (2), U12.2 (VSUPPLY); also elsewhere on the board
BIAS_REF: JP3.6; also elsewhere on the board
GND: ADXL375BCCZ.2 (GND), ADXL375BCCZ.4 (GND), ADXL375BCCZ.5 (GND), B1.3 (-), BMX055.4 (GNDA), BMX055.6 (GNDIO), BMX055.17 (SDO1), BMX055.20 (CSB3), C9.2, C12.2, C13.2, C14.2, C15.2, C16.2, C17.2, C18.2, C20.1, C21.1, CC2.P$6 (VSS), DS3231MZ+.5 (GND), JP1.2, JP3.4, MAX31725MTA+.4 (GND), MAX31725MTA+.5 (A2), MAX31725MTA+.6 (A1), MAX31725MTA+.7 (A0), MAX31725MTA+.9 (EP), MOTORDRIVER.P$3 (CAT), U12.1 (GND); also elsewhere on the board
MISO: JP1.3; also elsewhere on the board
MOSI: JP1.4; also elsewhere on the board
MOTOR: R2.2; also elsewhere on the board
MOTOR_GND: C1.2, C2.2, JP3.5, MOTORDRIVER.P$4 (GND)
MOTOR_SIGNAL: C2.1, JP3.3, MOTORDRIVER.P$5 (VO), R1.2
MOTOR_VCC: C1.1, JP3.1, MOTORDRIVER.P$6 (VCC), R1.1
unnamed: C20.2, CC2.P$5 (VCORE)
unnamed: MOTORDRIVER.P$1 (AN), R2.1
unnamed: MAX31725MTA+.3 (OS), R7.1
unnamed: B1.1 (+), B1.2 (+), C17.1, DS3231MZ+.6 (VBAT)
SCK: JP1.5; also elsewhere on the board
SCL: ADXL375BCCZ.14 (SCL/SCLK), BMX055.9 (SCX), CC2.P$4 (SCL), DS3231MZ+.8 (SCL), MAX31725MTA+.2 (SCL), R11.3 (1), U12.4 (SCL); also elsewhere on the board
SDA: ADXL375BCCZ.13 (SDA/SDI/SDIO), BMX055.11 (SDX), CC2.P$3 (SDA), DS3231MZ+.7 (SDA), MAX31725MTA+.1 (SDA), R11.4 (1), U12.3 (SDA); also elsewhere on the board

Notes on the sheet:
I2C PULLUPS
HIGH G ACCEL
TEMP SENSOR
REAL TIME CLOCK
IMU
HUMIDITY
I2C BUFFER
PRESSURE SENSOR
CONNECTOR
MOTOR DRIVER ISOLATER

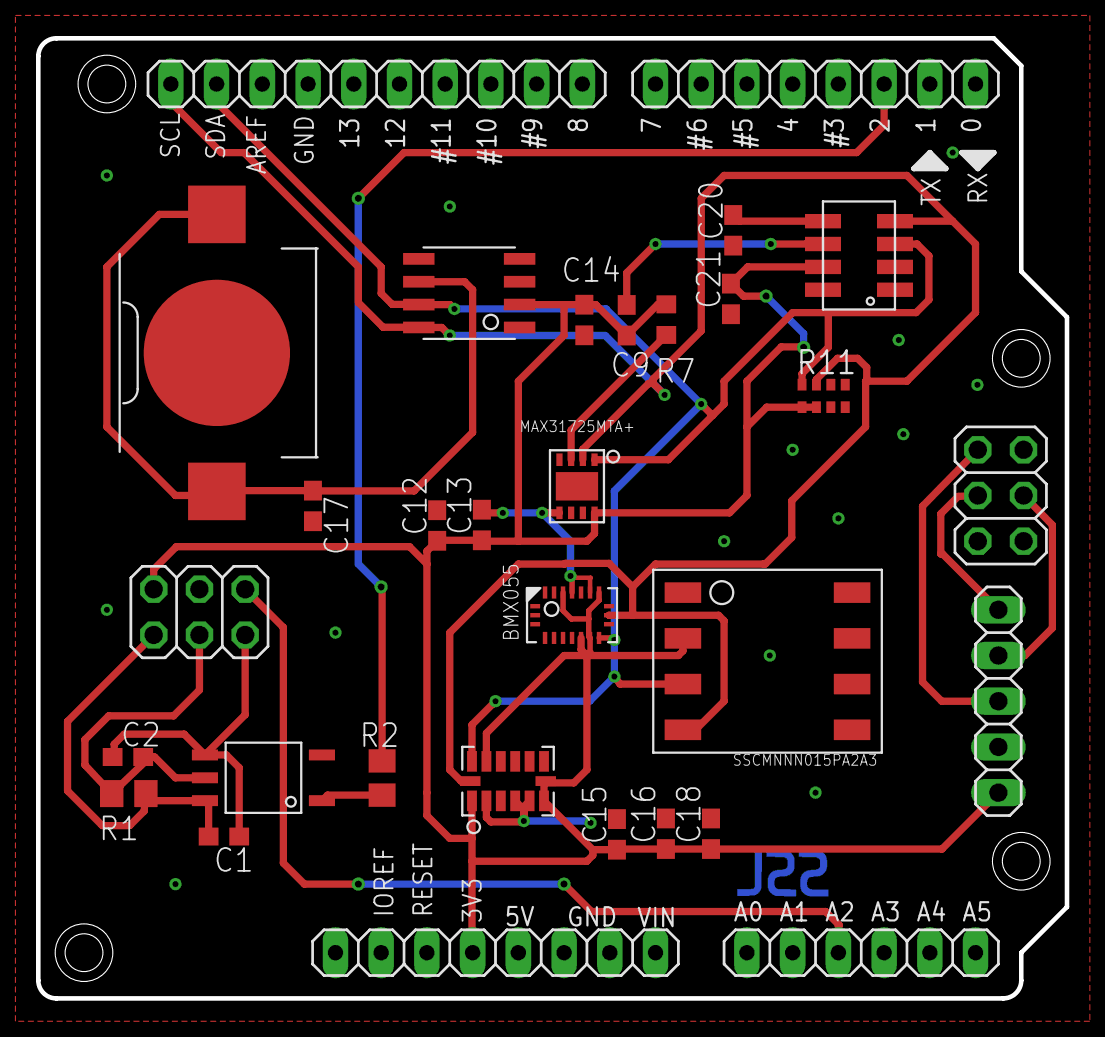
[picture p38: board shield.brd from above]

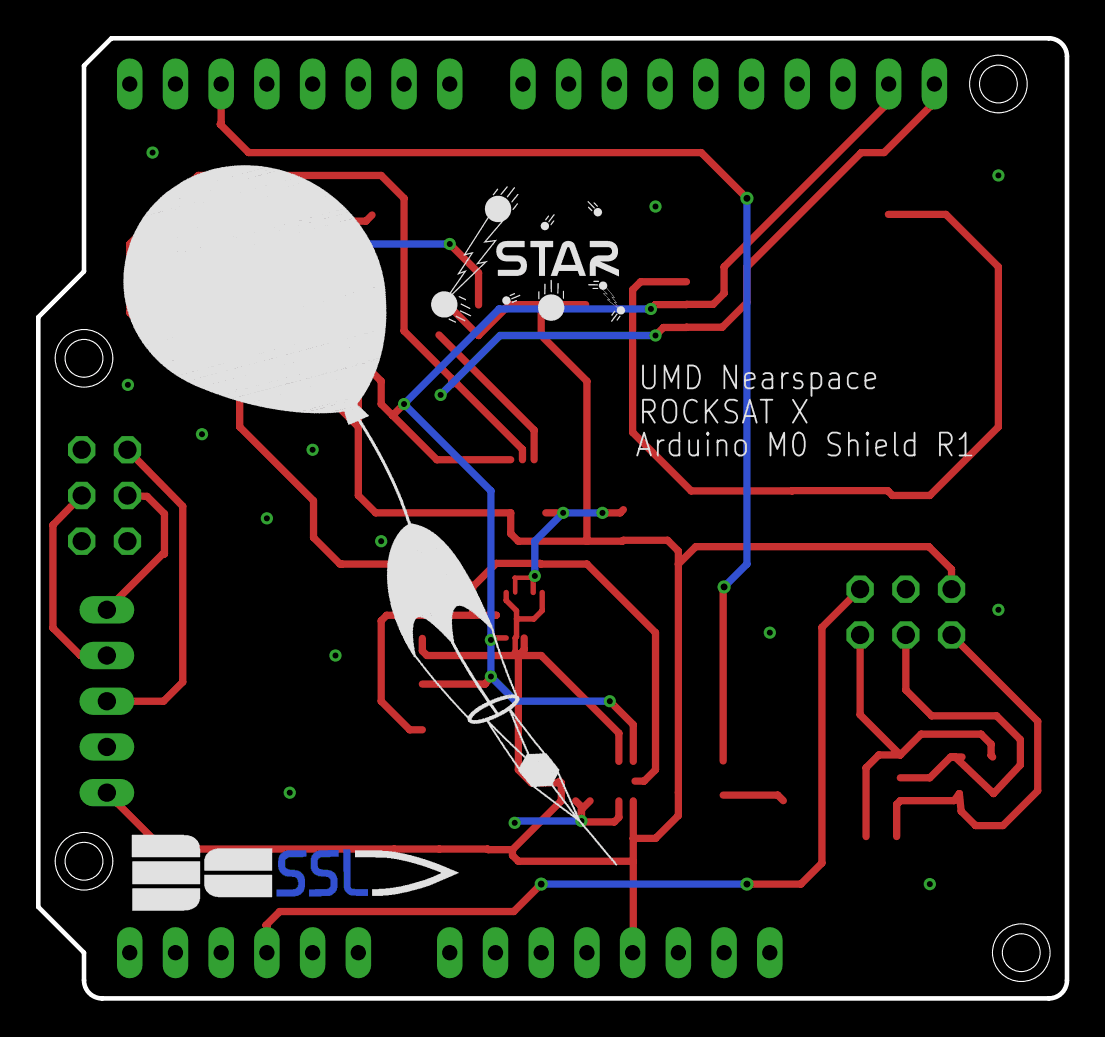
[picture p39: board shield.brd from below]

Board: 2 copper layers, 57.1 x 53.3 mm, 34 parts (3 on the bottom side), 16 nets.

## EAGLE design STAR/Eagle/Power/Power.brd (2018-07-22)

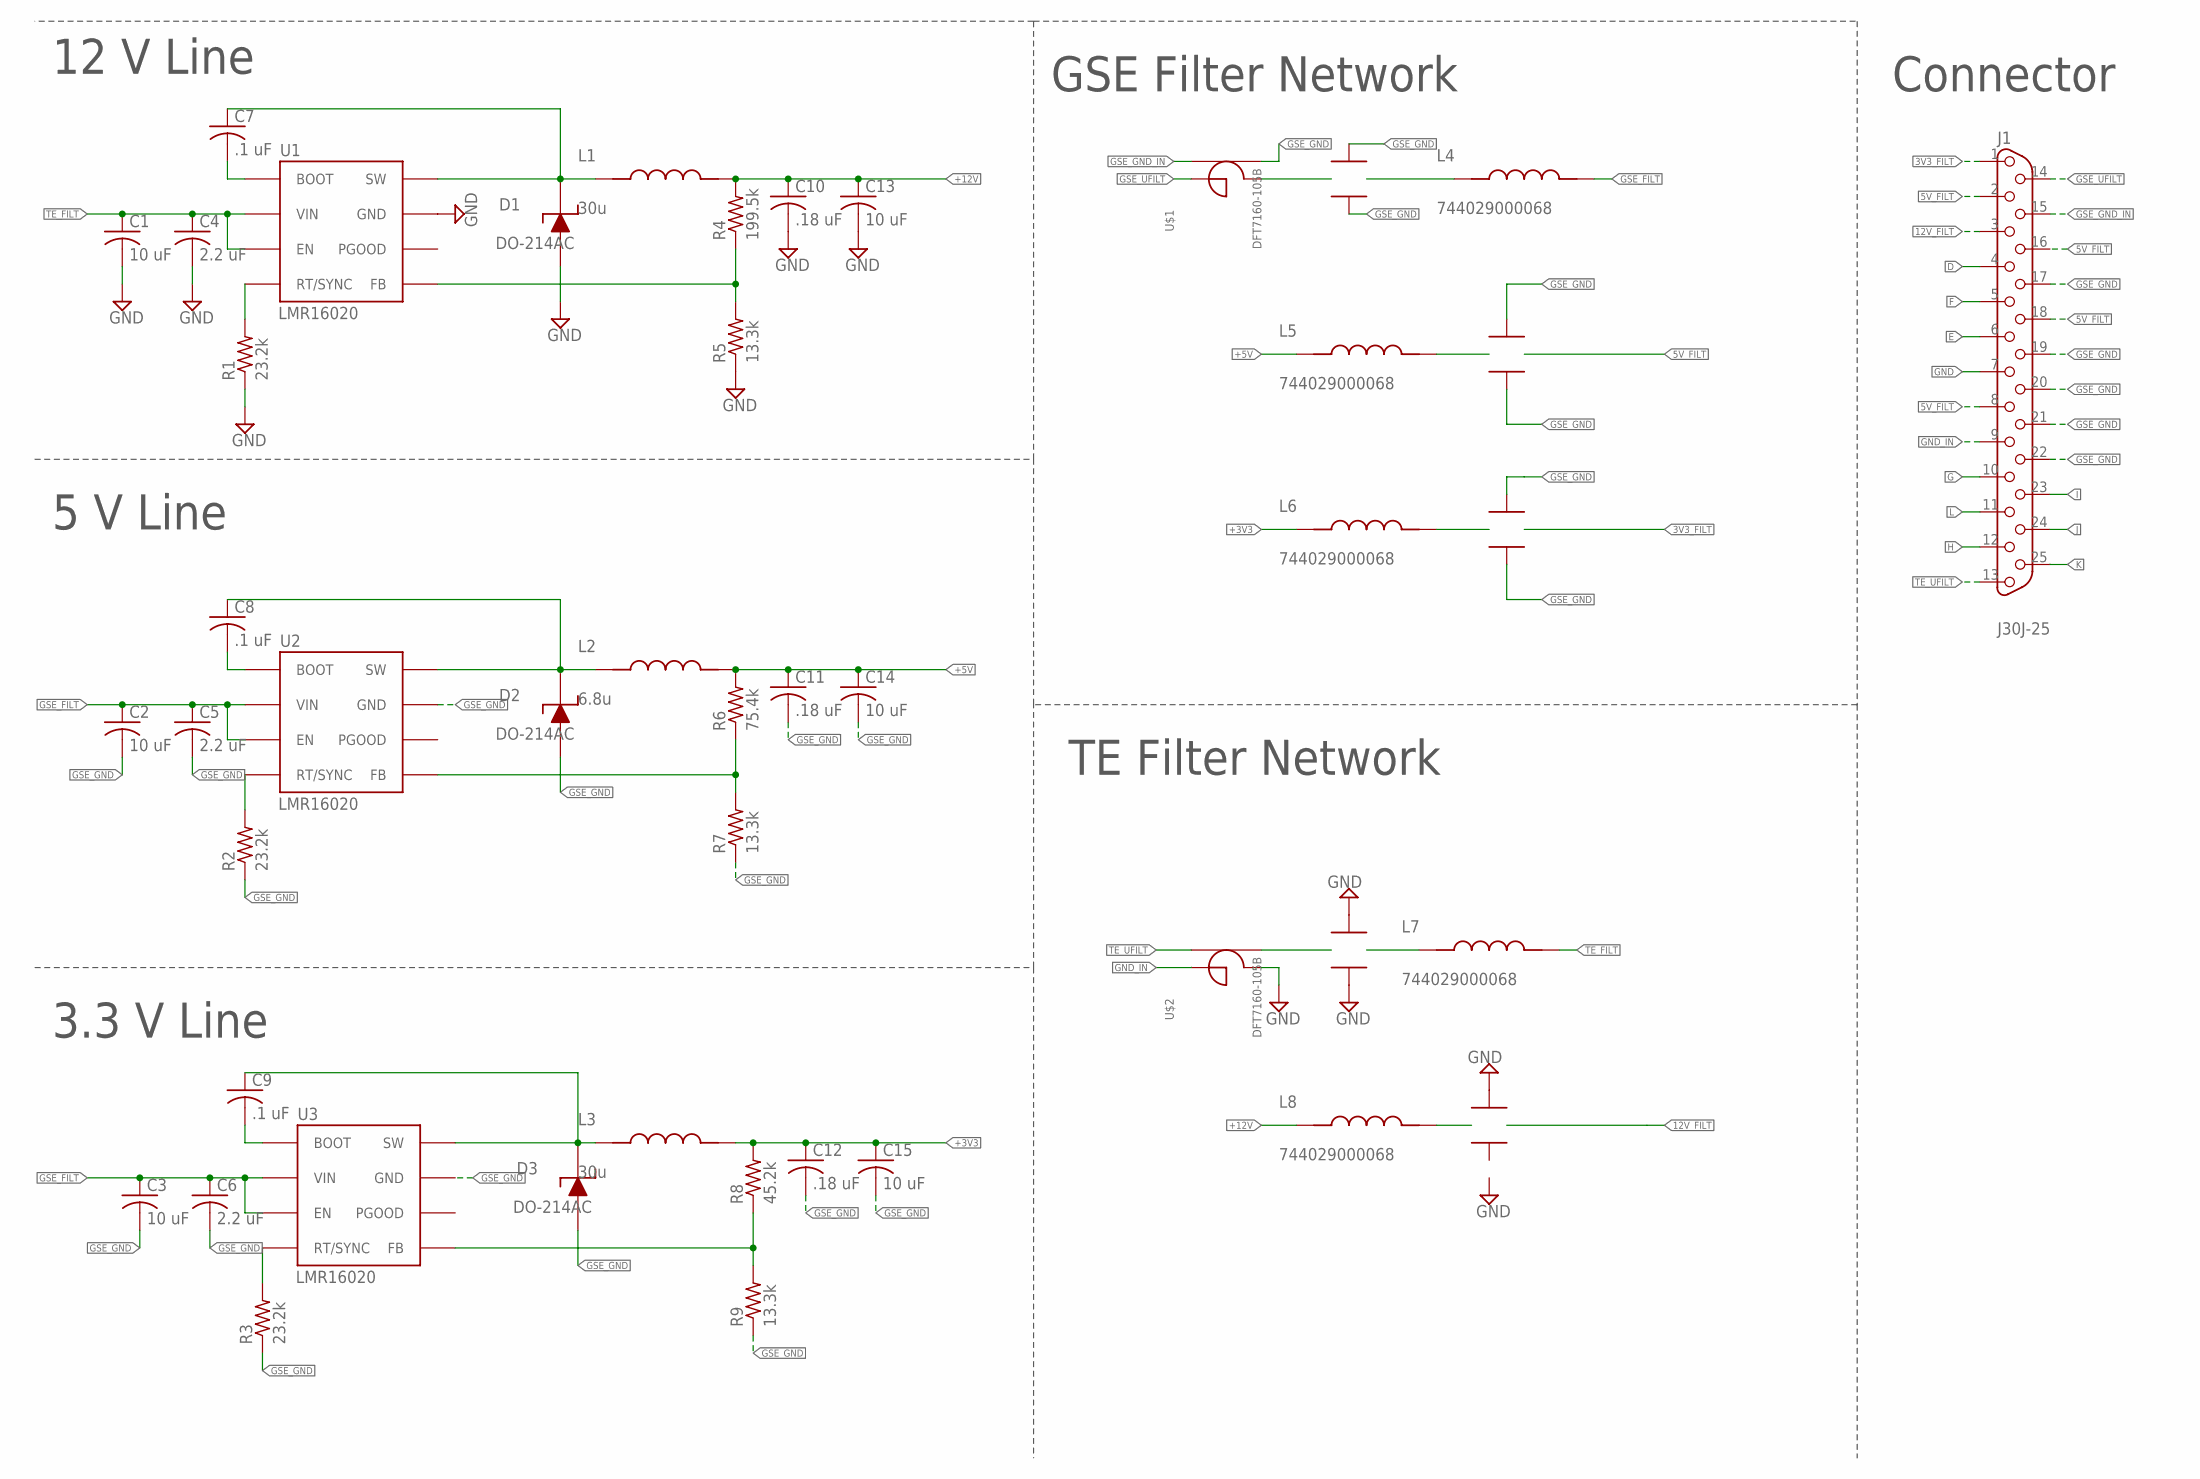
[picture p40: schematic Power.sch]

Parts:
C1, C2, C3: 10 uF; C1210
C4, C5, C6: 2.2 uF; C1210
C7, C8, C9: .1 uF; C0603
C10, C11, C12: .18 uF; C0603
C13, C14, C15: 10 uF; C0603
D1, D2, D3: DO-214AC
J1: J30J-25; ZKN-25
L1: 30u; 7050
L2: 6.8u; 7050
L3: 30u; 1365
L4, L5, L6, L7, L8: 744029000068; 2813
R1, R2, R3: 23.2k; R0603
R4: 199.5k; R0603
R5, R7, R9: 13.3k; R0603
R6: 75.4k; R0603
R8: 45.2k; R0603
U1, U2, U3: LMR16020; SO8
U$1, U$2: DFT7160-105B; DFT7160
U$3, U$4, U$5, U$6, U$7: 1410J0500404MXTE03; 1410

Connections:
3V3_FILT: J1.1, U$5.P$4
5V_FILT: J1.2, J1.8, J1.16, J1.18, U$4.P$4
12V_FILT: J1.3, U$7.P$4
+3V3: C12.1, C15.1, L3.P$2, L6.P$1, R8.2
+5V: C11.1, C14.1, L2.P$2, L5.P$1, R6.2
+12V: C10.1, C13.1, L1.P$2, L8.P$1, R4.2
D: J1.4
E: J1.6
F: J1.5
G: J1.10
GND: C1.2, C4.2, C10.2, C13.2, D1.P$1, J1.7, R1.1, R5.1, U1.P$7 (GND), U1.PAD (GND), U$2.P$4, U$6.P$2, U$6.P$3, U$7.P$3
GND_IN: J1.9, U$2.P$1
GSE_FILT: C2.1, C3.1, C5.1, C6.1, L4.P$2, U2.P$2 (VIN), U2.P$3 (EN), U3.P$2 (VIN), U3.P$3 (EN)
GSE_GND: C2.2, C3.2, C5.2, C6.2, C11.2, C12.2, C14.2, C15.2, D2.P$1, D3.P$1, J1.17, J1.19, J1.20, J1.21, J1.22, R2.1, R3.1, R7.1, R9.1, U2.P$7 (GND), U2.PAD (GND), U3.P$7 (GND), U3.PAD (GND), U$1.P$3, U$3.P$2, U$3.P$3, U$4.P$2, U$4.P$3, U$5.P$2, U$5.P$3
GSE_GND_IN: J1.15, U$1.P$2
GSE_UFILT: J1.14, U$1.P$1
H: J1.12
I: J1.23
J: J1.24
K: J1.25
L: J1.11
unnamed: R3.2, U3.P$4 (RT/SYNC)
unnamed: C9.1, D3.P$2, L3.P$1, U3.P$8 (SW)
unnamed: R2.2, U2.P$4 (RT/SYNC)
unnamed: C8.2, U2.P$1 (BOOT)
unnamed: C8.1, D2.P$2, L2.P$1, U2.P$8 (SW)
unnamed: C9.2, U3.P$1 (BOOT)
unnamed: R1.2, U1.P$4 (RT/SYNC)
unnamed: R8.1, R9.2, U3.P$5 (FB)
unnamed: R6.1, R7.2, U2.P$5 (FB)
unnamed: C7.2, U1.P$1 (BOOT)
unnamed: C7.1, D1.P$2, L1.P$1, U1.P$8 (SW)
unnamed: R4.1, R5.2, U1.P$5 (FB)
unnamed: U$1.P$4, U$3.P$4
unnamed: U$2.P$3, U$6.P$5
unnamed: L4.P$1, U$3.P$5
unnamed: L5.P$2, U$4.P$5
unnamed: L6.P$2, U$5.P$5
unnamed: L7.P$1, U$6.P$4
unnamed: L8.P$2, U$7.P$5
TE_FILT: C1.1, C4.1, L7.P$2, U1.P$2 (VIN), U1.P$3 (EN)
TE_UFILT: J1.13, U$2.P$2

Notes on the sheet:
12 V Line
5 V Line
3.3 V Line
GSE Filter Network
TE Filter Network
Connector

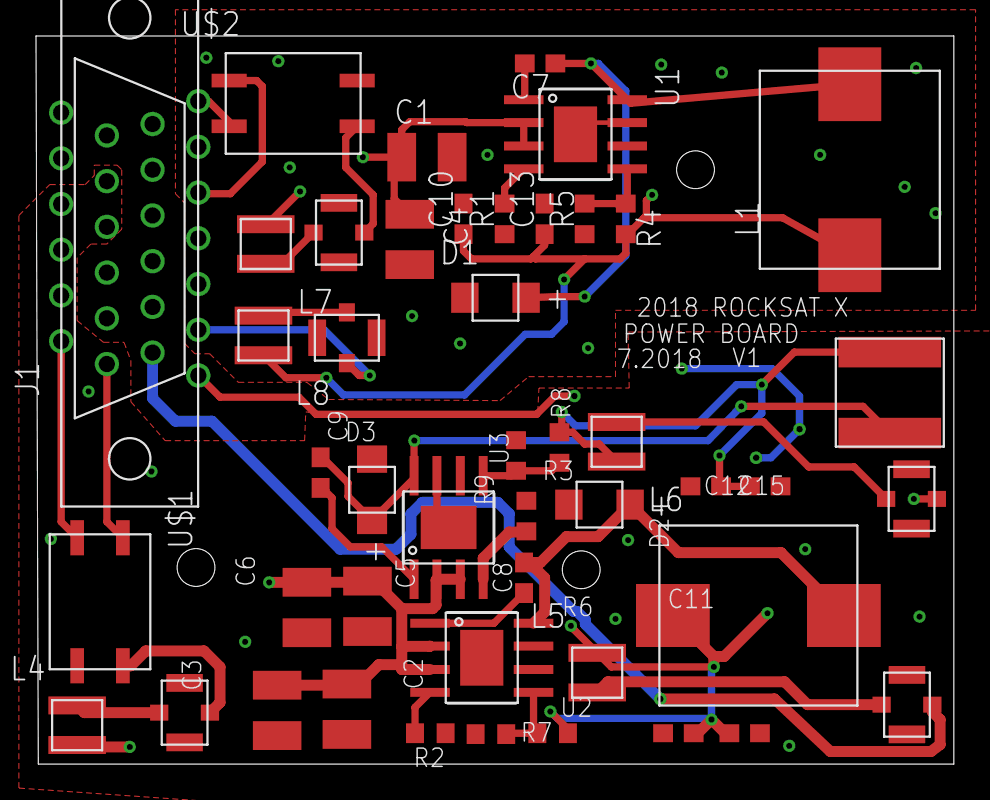
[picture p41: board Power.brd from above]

Board: 2 copper layers, 51.0 x 40.4 mm, 46 parts (0 on the bottom side), 33 nets.

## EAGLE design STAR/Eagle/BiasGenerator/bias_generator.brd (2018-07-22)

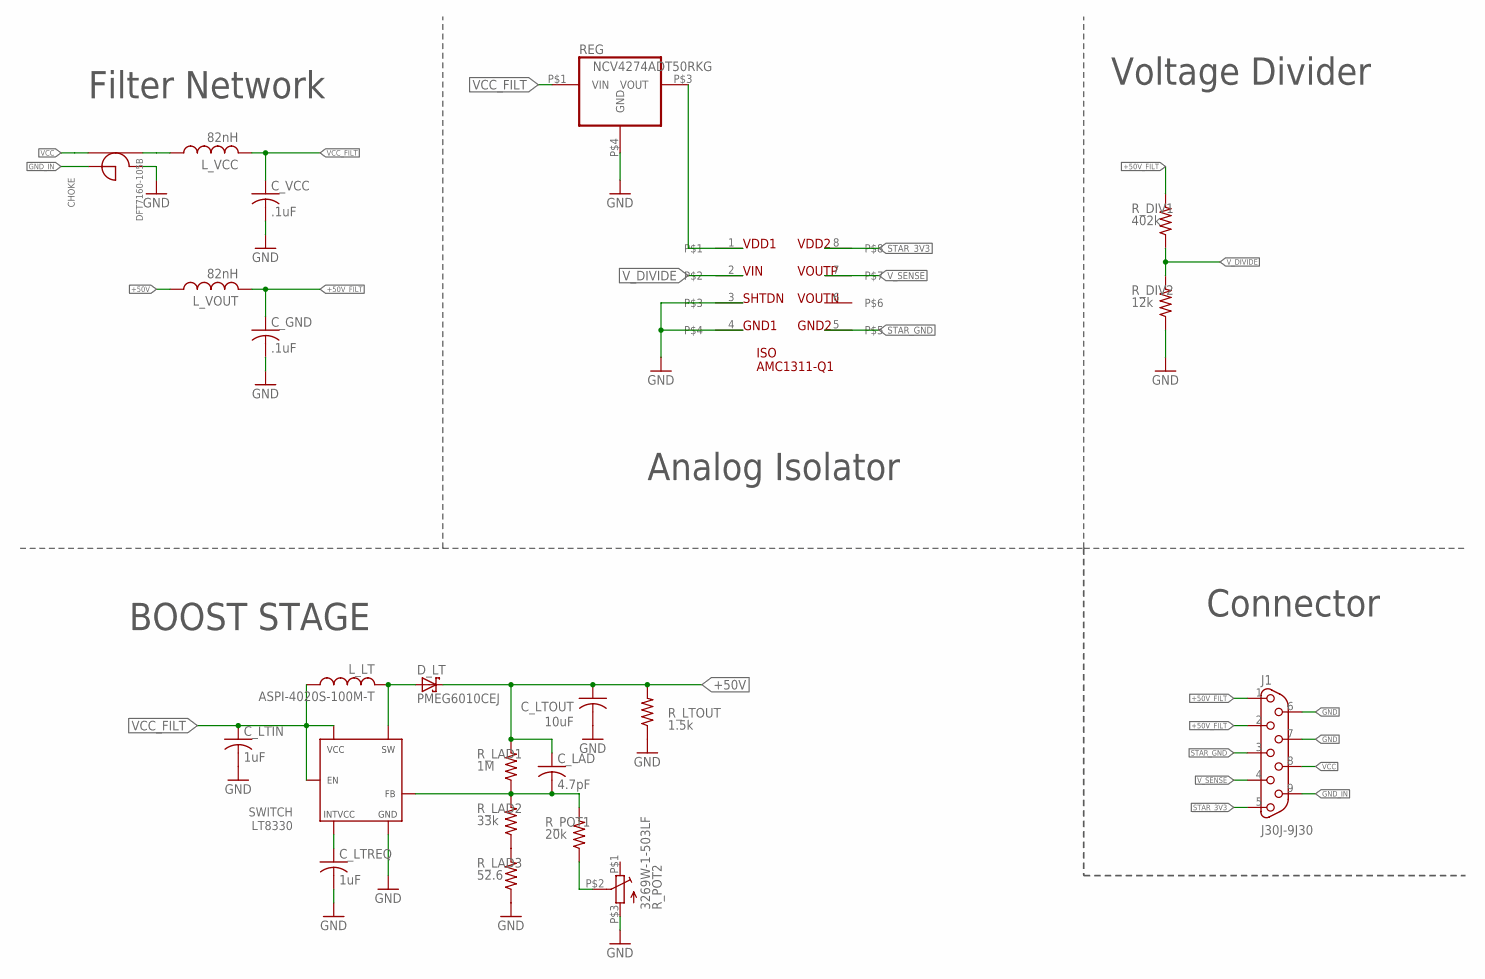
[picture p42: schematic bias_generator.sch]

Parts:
CHOKE: DFT7160-105B; DFT7160
C_GND: .1uF; C0603
C_LAD: 4.7pF; 0603
C_LTIN: 1uF; 0603
C_LTOUT: 10uF; 2J-LEAD
C_LTREQ: 1uF; 0603
C_VCC: .1uF; C0603
D_LT: PMEG6010CEJ; SOD323
ISO: AMC1311-Q1; SOIC8
J1: J30J-9J30; ZKN-9-J30
L_LT: ASPI-4020S-100M-T; 4MM
L_VCC: 82nH; C0603
L_VOUT: 82nH; C0603
REG: NCV4274ADT50RKG; DPAK
R_DIV1: 402k; R0603
R_DIV2: 12k; R0603
R_LAD1: 1M; R0603
R_LAD2: 33k; R0603
R_LAD3: 52.6; R0603
R_LTOUT: 1.5k; R2512
R_POT1: 20k; R0603
R_POT2: 3269W-1-503LF; POTENTIOMETER
SWITCH: LT8330; 8-DFN

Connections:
5V_REG: ISO.1, REG.P$3 (VOUT)
+50V: C_LAD.1, C_LTOUT.P$1 (1), D_LT.P$2 (C), L_VOUT.1, R_LAD1.2, R_LTOUT.2
+50V_FILT: C_GND.1, J1.1, J1.2, L_VOUT.2, R_DIV1.2
FBX: C_LAD.2, R_LAD1.1, R_LAD2.2, R_POT1.2, SWITCH.P$1 (FB)
GND: CHOKE.P$4 (L1OUT), C_GND.2, C_LTIN.2, C_LTOUT.P$2 (2), C_LTREQ.2, C_VCC.2, ISO.3, ISO.4, J1.6, J1.7, REG.P$4 (GND), R_DIV2.1, R_LAD3.1, R_LTOUT.1, R_POT2.P$3, SWITCH.P$5 (GND), SWITCH.P$9 (GND)
GND_IN: CHOKE.P$1 (L1IN), J1.9
INTVCC: C_LTREQ.1, SWITCH.P$7 (INTVCC)
unnamed: CHOKE.P$3 (L2OUT), L_VCC.1
unnamed: R_POT1.1, R_POT2.P$2
unnamed: R_LAD2.1, R_LAD3.2
STAR_3V3: ISO.8, J1.5
STAR_GND: ISO.5, J1.3
SW: D_LT.P$1 (A), L_LT.P$2 (2), SWITCH.P$3 (SW), SWITCH.P$4 (SW)
VCC: CHOKE.P$2 (L2IN), J1.8
VCC_FILT: C_LTIN.1, C_VCC.1, L_LT.P$1 (1), L_VCC.2, REG.P$1 (VIN), SWITCH.P$6 (VCC), SWITCH.P$8 (EN)
V_DIVIDE: ISO.2, R_DIV1.1, R_DIV2.2
V_SENSE: ISO.7, J1.4

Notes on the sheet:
BOOST STAGE
Voltage Divider
Connector
Filter Network
Analog Isolator

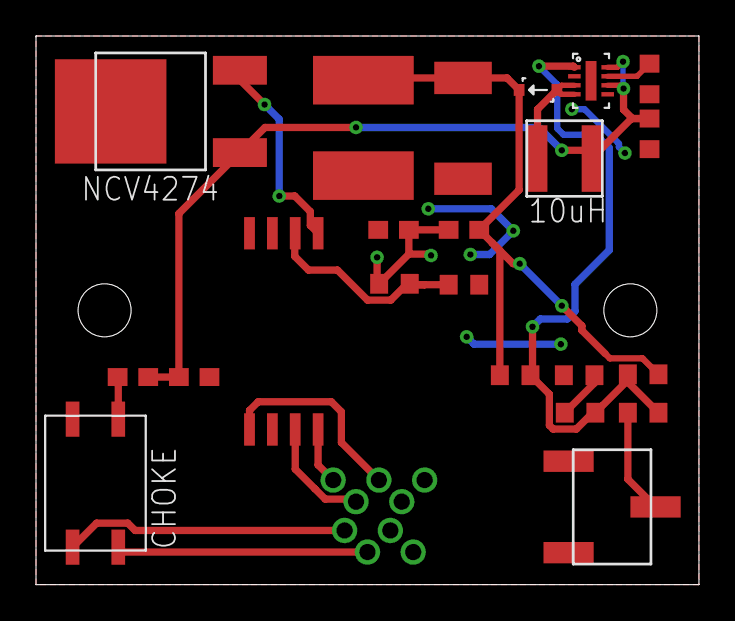
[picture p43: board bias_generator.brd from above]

Board: 2 copper layers, 36.8 x 30.5 mm, 23 parts (0 on the bottom side), 17 nets.

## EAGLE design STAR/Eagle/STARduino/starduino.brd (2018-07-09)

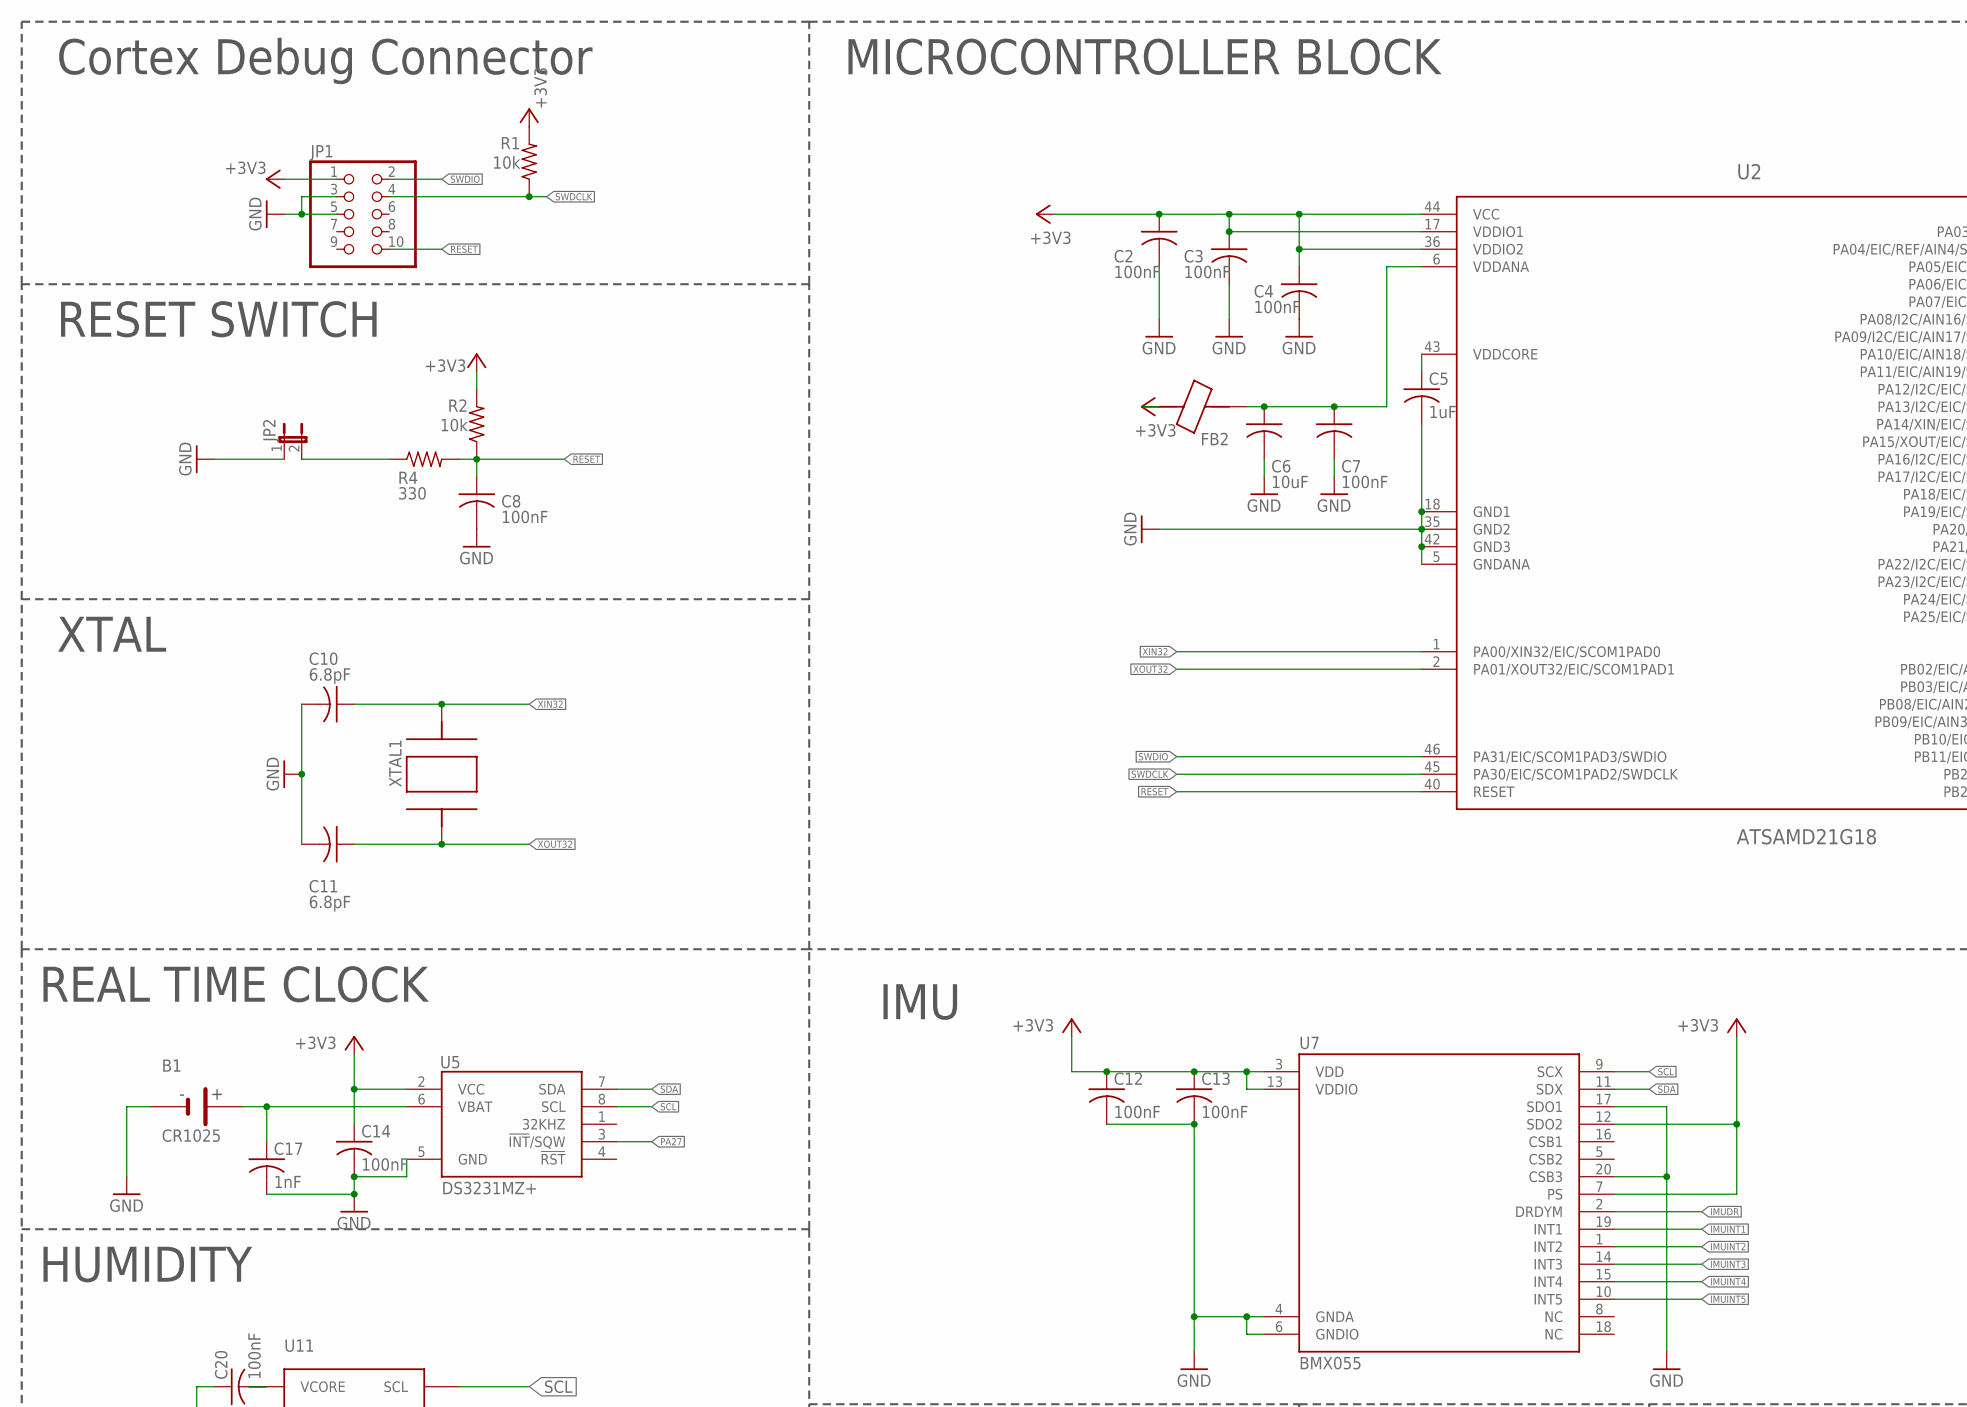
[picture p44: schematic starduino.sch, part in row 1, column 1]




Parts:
B1: CR1025
C1, C2, C3, C4, C7, C8, C9, C12, C13, C14, C16, C18, C20: 100nF; C0603
C5: 1uF; C0603
C6, C15: 10uF; C0603
C10, C11: 6.8pF; C0603
C17: 1nF; C0603
C19: 100pF; C0603
C21: 220nF; C0603
FB1, FB2: BLM18KG221BH1D; 0603
IMAG1: SSL.3IN_SILK; SSL_SILK_.3IN
IMAG2: STAR; STAR_.3IN
J1: J30J-9J30J; ZKN-9
JP1: PINHD-2X5; 2X05
JP2: JUMPER-2PTH; 1X02
JP3: PINHD-2X3; 2X03
R1, R2: 10k; R0603
R3, R9, R10: 4.7k; R0603
R4: 330; R0603
R5: 3.6k; R0603
R6: 6.8k; R0603
R7: 4.7k; 0603-ARV
R8: 220k; R0603
U1: PCA9515A; TSSOP8
U2: ATSAMD21G18; 48-TQFP
U3: MAX31725MTA+; DFN-8
U4: MC74VHC1GT125; SC-70-5
U5: DS3231MZ+; SOIC-8
U6: MC14504BDTG; TSSOP16
U7: BMX055; LGA-20
U8: ADXL375BCCZ; LGA-14
U9: TCA9535_RTW_24; RTW24_2P45X2P45
U10: PCA9306DCT; SSOP8
U11: CC2
U12: SSCMNNN015PA2A3; HSC-SMT-8
U$1: FODM8061-D; SO5
XTAL1: ABS07AIG-32.768KHZ-1-T; 2-SMD

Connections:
5V_S: R5.1, R8.2, R9.2, R10.2, U6.16 (VDD), U9.18 (A0), U9.21 (VCC), U9.23 (A1), U9.24 (A2)
+3V3: C2.1, C3.1, C4.1, C9.1, C12.1, C13.1, C14.1, C15.1, C16.1, C18.1, C21.2, FB1.2, FB2.1, J1.6, J1.8, JP1.1, JP3.2, R1.2, R2.2, R3.2, R7.5 (2), R7.6 (2), R7.7 (2), R7.8 (2), U1.P$8 (VCC), U2.17 (VDDIO1), U2.36 (VDDIO2), U2.44 (VCC), U3.8 (VDD), U4.5 (VIN), U5.2 (VCC), U6.1 (VCC), U7.3 (VDD), U7.7 (PS), U7.12 (SDO2), U7.13 (VDDIO), U8.1 (VDDIO), U8.6 (VS), U8.7 (!CS!), U8.12 (SDO/ADDR), U10.2 (VREF1), U11.P$7 (VDD), U12.2 (VSUPPLY)
BIAS_REF: JP3.6, U2.7 (PB08/EIC/AIN2/SCOM4PAD0/TC4)
GND: B1.3 (-), C1.2, C2.2, C3.2, C4.2, C5.2, C6.2, C7.2, C8.2, C9.2, C10.2, C11.2, C12.2, C13.2, C14.2, C15.2, C16.2, C17.2, C18.2, C19.2, C20.1, C21.1, J1.5, J1.7, JP1.3, JP1.5, JP2.1, JP3.4, R6.2, U1.P$4 (GND), U2.5 (GNDANA), U2.18 (GND1), U2.35 (GND2), U2.42 (GND3), U3.4 (GND), U3.5 (A2), U3.6 (A1), U3.7 (A0), U3.9 (EP), U4.1 (OE), U4.3 (GND), U5.5 (GND), U6.8 (VSS), U6.13 (MODE), U7.4 (GNDA), U7.6 (GNDIO), U7.17 (SDO1), U7.20 (CSB3), U8.2 (GND), U8.4 (GND), U8.5 (GND), U9.9 (GND), U9.25 (EPAD), U10.1 (GND), U11.P$6 (VSS), U12.1 (GND), U$1.P$3 (CAT)
IMUDR: U6.9 (DIN), U7.2 (DRDYM)
IMUINT1: U6.5 (BIN), U7.19 (INT1)
IMUINT2: U6.7 (CIN), U7.1 (INT2)
IMUINT3: U6.3 (AIN), U7.14 (INT3)
IMUINT4: U6.11 (EIN), U7.15 (INT4)
IMUINT5: U6.14 (FIN), U7.10 (INT5)
IOEINT: U2.26 (PA17/I2C/EIC/SCOM1PAD1+/TC2), U4.4 (Y)
MISO: J1.2, U2.21 (PA12/I2C/EIC/SCOM2PAD0+/TC2)
MOSI: J1.1, U2.19 (PB10/EIC/SCOM4PAD2/TC5)
MOTOR: U2.10 (PA05/EIC/AIN5/SCOM0PAD1), U$1.P$1 (AN)
MOTOR_GND: JP3.5, U$1.P$4 (GND)
MOTOR_SIGNAL: JP3.3, U$1.P$5 (VO)
MOTOR_VCC: JP3.1, U$1.P$6 (VCC)
unnamed: C20.2, U11.P$5 (VCORE)
unnamed: C5.1, U2.43 (VDDCORE)
unnamed: R3.1, U3.3 (OS)
unnamed: JP2.2, R4.1
unnamed: B1.1 (+), B1.2 (+), C17.1, U5.6 (VBAT)
unnamed: C6.1, C7.1, FB2.2, U2.6 (VDDANA)
unnamed: U6.2 (AOUT), U9.1 (P00)
unnamed: U6.4 (BOUT), U9.2 (P01)
unnamed: U4.2 (A), U9.22 (INT)
unnamed: U6.6 (COUT), U9.3 (P02)
unnamed: U6.10 (DOUT), U9.4 (P03)
unnamed: U6.12 (EOUT), U9.5 (P04)
unnamed: U6.15 (FOUT), U9.6 (P05)
unnamed: R10.1, U9.20 (SDA), U10.8 (SDA2)
unnamed: R9.1, U9.19 (SCL), U10.7 (SCL2)
unnamed: C19.1, R8.1, U10.5 (EN), U10.6 (VREF2)
PA27: U2.39 (PA27/EIC), U5.3 (!INT!/SQW)
PB02: U2.47 (PB02/EIC/AIN10/SCOM5PAD0), U8.8 (INT1)
PB03: U2.48 (PB03/EIC/AIN11/SCOM5PAD1), U8.9 (INT2)
RESET: C8.1, JP1.10, R2.1, R4.2, U2.40 (RESET)
SCK: J1.3, U2.20 (PB11/EIC/SCOM4PAD3/TC5)
SCL: R7.3 (1), U1.P$2 (SCL0), U2.32 (PA23/I2C/EIC/SCOM5PAD1+/TC4), U3.2 (SCL), U5.8 (SCL), U7.9 (SCX), U8.14 (SCL/SCLK), U10.3 (SCL1), U11.P$4 (SCL), U12.4 (SCL)
SCL_BUFF: R7.2 (1), U1.P$7 (SCL1)
SDA: R7.4 (1), U1.P$3 (SDA0), U2.31 (PA22/I2C/EIC/SCOM5PAD0+/TC4), U3.1 (SDA), U5.7 (SDA), U7.11 (SDX), U8.13 (SDA/SDI/SDIO), U10.4 (SDA1), U11.P$3 (SDA), U12.3 (SDA)
SDA_BUFF: R7.1, U1.P$6 (SDA1)
SWDCLK: JP1.4, R1.1, U2.45 (PA30/EIC/SCOM1PAD2/SWDCLK)
SWDIO: JP1.2, U2.46 (PA31/EIC/SCOM1PAD3/SWDIO)
VREFA: C1.1, FB1.1, U2.4 (PA03/EIC/REF/AI/VREFA)
V_SENSE: R5.2, R6.1, U2.3 (PA02/EIC/AIN)
XIN32: C10.1, U2.1 (PA00/XIN32/EIC/SCOM1PAD0), XTAL1.P2 (2)
XOUT32: C11.1, U2.2 (PA01/XOUT32/EIC/SCOM1PAD1), XTAL1.P1 (1)

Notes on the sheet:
MICROCONTROLLER BLOCK
Cortex Debug Connector
RESET SWITCH
XTAL
AREF
V SENSE
I2C PULLUPS
HIGH G ACCEL
TEMP SENSOR
REAL TIME CLOCK
IMU
HUMIDITY
MULTIPLEXER
I2C BUFFER
PRESSURE SENSOR
CONNECTOR
MOTOR DRIVER ISOLATER



Board: 2 copper layers, 59.7 x 44.6 mm, 54 parts (2 on the bottom side), 48 nets.

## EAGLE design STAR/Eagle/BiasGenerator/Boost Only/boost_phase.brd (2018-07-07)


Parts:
C1, C2: 1uF; C0805
C3: 4.7pF; C0805
C4: 10uF; 2J-LEAD
D1: PMEG6010ETR; SOD123
JP1, JP2: SCREWTERM_1X2
L1: 10uH; PQ2614
R1: 1M; R0805
R2: 33k; R0805
R3: 52.3; R0805
R4: 1.5k; R2512
U1: LT8330SOT23-6; SOT23-6

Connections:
+50V: C3.1, C4.P$1 (1), D1.P$2 (C), JP2.1, R1.2, R4.2
GND: C1.2, C2.2, C4.P$2 (2), JP1.2, JP2.2, R3.1, R4.1, U1.2 (GND)
unnamed: C2.1, U1.5 (INTVCC)
unnamed: R2.1, R3.2
unnamed: D1.P$1 (A), L1.P$3 (2), U1.1 (SW)
unnamed: C3.2, R1.1, R2.2, U1.3 (FB)
VCC: C1.1, JP1.1, L1.P$2 (1), U1.4 (EN), U1.6 (VCC)

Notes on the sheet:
BOOST STAGE
Connector


Board: 2 copper layers, 34.0 x 40.8 mm, 13 parts (0 on the bottom side), 7 nets.

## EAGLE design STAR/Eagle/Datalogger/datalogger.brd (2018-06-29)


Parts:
C1, C3, C6, C7, C9: 0.1uF; C0603
C2, C4, C5, C8, C10: 10nF; C0603
GND1: SSL.3IN_SILK; SSL_SILK_.3IN
J1: J30J-25; ZKN-25
R2: 1M; R0603
U$1: MICRO_SD; MICRO_SD_HINGED
U$2, U$3: USB_A

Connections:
+3V3: C1.1, C2.1, J1.13, R2.2, U$1.VDD
+5V1: C3.1, C4.1, J1.4, U$2.VCC1
+5V2: C5.1, C6.1, J1.22, U$2.VCC2
+5V3: C9.1, C10.1, J1.17, U$3.VCC1
+5V4: C7.1, C8.1, J1.19, U$3.VCC2
CS_STAR: R2.1, U$1.CD
DATA1_N: J1.2, U$2.DATA+1 (DATA-1)
DATA1_P: J1.1, U$2.DATA-1 (DATA+1)
DATA2_N: J1.23, U$2.DATA+2 (DATA-2)
DATA2_P: J1.25, U$2.DATA-2 (DATA+2)
DATA3_N: J1.15, U$3.DATA+1 (DATA-1)
DATA3_P: J1.14, U$3.DATA-1 (DATA+1)
DATA4_N: J1.20, U$3.DATA+2 (DATA-2)
DATA4_P: J1.21, U$3.DATA-2 (DATA+2)
GND: C1.2, C2.2, J1.11, U$1.CD1, U$1.GND1 (G1), U$1.GND2 (G2), U$1.GND3 (G3), U$1.GND4 (G4), U$1.VSS
GND1: C3.2, C4.2, J1.3, J1.5, U$2.GND1
GND2: C5.2, C6.2, J1.8, J1.9, U$2.GND2
GND3: C9.2, C10.2, J1.16, J1.18, U$3.GND1
GND4: C7.2, C8.2, J1.6, J1.7, U$3.GND2
MISO_STAR: J1.12, U$1.DAT0
MOSI_STAR: J1.24, U$1.CMD
SCK_STAR: J1.10, U$1.CLK

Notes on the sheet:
PI 1/2
PI 3/4
SD CARD
CONNECTOR



Board: 2 copper layers, 28.4 x 56.2 mm, 16 parts (10 on the bottom side), 22 nets.

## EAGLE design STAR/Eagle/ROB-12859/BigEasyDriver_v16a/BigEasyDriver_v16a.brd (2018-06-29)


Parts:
3/5V: SOLDERJUMPERNO; SJ_2S-NO
APWR: SOLDERJUMPERTRACE; SJ_2S-TRACE
C1: .1uF; 0603-CAP
C2: 1uF; 0603-CAP
C6, C7, C8, C9, C11: .1uf; 0603-CAP
C10: .22uF; 0603-CAP
C14: 47uF; PANASONIC_D
D1: B340A-13-F; DO-214AC
FID1, FID2: FIDUCIAL1X2; FIDUCIAL-1X2
FRAME1: FRAME-LETTER; CREATIVE_COMMONS
IC1: A4988ALT1; QFN-28-5MM_ALT1
IC2: LM317L; SCHMALZHAUS_SOT89
JP1, JP6: M02PTH; 1X02
JP3, JP10, JP14: M04PTH; 1X04
JP5, JP11, JP12: M04SCREW_LOCK; SCREWTERMINAL-3.5MM-4_LOCK
JP7, JP13: M023.5MM_LOCK; SCREWTERMINAL-3.5MM-2_LOCK
JP8, JP9: STAND-OFF
LOGO1: OSHW_LOGO_FILLX0100-NT; OSHW_FILLX100_NOTEXT
PWR_LED: YELLOW; LED-0603
R1, R2, R3, R4, R5, R10, R11, R12, R20: 20K; 0603-RES
R6: 390; 0603-RES
R7: 330; 0603-RES
R8: 240; 0603-RES
R9, R14, R15: 1K; 0603-RES
R13: 8.2K; 0603-RES
R16: 10K; TRIMPOT-3MM-2
R18, R19: .11; R2010
TP1: TPPAD1-13; P1-13
U$2: LOGO-SFENEW; SFE-NEW-WEBLOGO
U$3, U$4, U$5: PAD; PAD-0.008

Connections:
5V_ALT: APWR.1, IC2.OUT, IC2.OUT@1 (OUT), R8.2
COILA+: IC1.P$21 (OUT1B), JP3.4, JP5.4
COILA-: IC1.P$24 (OUT1A), JP3.3, JP5.3
COILB+: IC1.P$1 (OUT2B), JP3.1, JP5.1
COILB-: IC1.P$26 (OUT2A), JP3.2, JP5.2
CUR_REF: IC1.P$17 (REF), R16.2 (WIPER), TP1.TP
DIR: IC1.P$19 (DIR), R11.1, R14.2
DIR_IN: JP12.4, JP14.4, R14.1
ENABLE: IC1.P$2 (ENABLE), JP6.1, JP13.1, R10.1
GND: 3/5V.2, C1.2, C2.2, C7.2, C8.2, C9.2, C10.2, C14.-, IC1.P$3 (GND), IC1.P$18 (GND), IC1.P$29 (GND_PAD), JP1.1, JP7.1, JP12.2, JP14.2, PWR_LED.C, R7.1, R10.2, R16.3 (CW), R18.1, R19.1, R20.2
MS1: IC1.P$9 (MS1), JP6.2, JP13.2, R1.1
MS2: IC1.P$10 (MS2), JP10.1, JP11.1, R2.1
MS3: IC1.P$11 (MS3), JP10.2, JP11.2, R3.1
unnamed: D1.A, JP1.2, JP7.2
unnamed: PWR_LED.A, R9.1
unnamed: R13.2, R16.1 (CCW)
unnamed: 3/5V.1, R6.1, R7.2
unnamed: IC1.P$7 (NC), U$3.P$1
unnamed: IC2.ADJ, R6.2, R8.1
unnamed: IC1.P$20 (NC), U$4.P$1
unnamed: C6.1, IC1.P$4 (CP1)
unnamed: C6.2, IC1.P$5 (CP2)
unnamed: IC1.P$25 (NC), U$5.P$1
unnamed: IC1.P$13 (ROSC), R20.1
unnamed: C10.1, IC1.P$8 (VREG)
unnamed: C11.1, IC1.P$6 (VCP)
unnamed: IC1.P$27 (SENSE2), R18.2
unnamed: IC1.P$23 (SENSE1), R19.2
RESET: IC1.P$12 (RESET), JP10.3, JP11.3, R5.1
SLEEP: IC1.P$14 (SLEEP), JP10.4, JP11.4, R4.1
STEP: IC1.P$16 (STEP), R12.1, R15.2
STEP_IN: JP12.3, JP14.3, R15.1
V+: C1.1, C8.1, C9.1, C11.2, C14.+, D1.C, IC1.P$22 (VBB1), IC1.P$28 (VBB2), IC2.IN
VCC: APWR.2, C2.1, C7.1, IC1.P$15 (VDD), JP12.1, JP14.1, R1.2, R2.2, R3.2, R4.2, R5.2, R9.2, R11.2, R12.2, R13.1

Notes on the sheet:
Brian Schmalz
Produced by SparkFun Electronics
v16a
Revised by Patrick Alberts


Board: 4 copper layers, 36.8 x 30.5 mm, 56 parts (1 on the bottom side), 34 nets.

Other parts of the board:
U$1: SCHMALZHAUS_SMALL

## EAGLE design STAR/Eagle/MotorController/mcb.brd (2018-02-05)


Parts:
C1, C2, C12, C13, C14, C15, C18, C21: 1uF; C0603
C3, C9, C10, C11, C17: 10uF; C1206
C4, C5: 2.2uF; C0805
C6: 5nF; C0603
C7, C16, C19, C20: 100nF; C0603
C8: 10pF; C0603
C22: 22pF; C0603
J1: J30J-9J30; ZKN-9-J30
JP1: PINHD-2X3; 2X03
JP2: JUMPER-2SMD-NO; SJ_2S-NO
L1: 22uH; SRP1265A
R1: 8.66k; R0603
R2: 1M; R0603
R3: 71.5k; R0603
R4: 51.1k; R0603
R5: 20k; R0603
R6: 4.7k; R0603
R7, R8: 1.24; R0603
U1: ATMEGA328P-MU; QFN50P500X500X100-33N
U2: A4988SETTR-T; QFN50P500X500X100-29N
U3: LT3010; 8-MSOP
U4: LT8630; 20-TSSOP

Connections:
+5V: C2.1, C12.1, C13.1, C14.1, C15.1, C18.1, C21.1, JP1.2, R6.2, U1.4 (VCC), U1.6 (VCC_2), U1.18 (AVCC), U1.20 (AREF), U2.14 (~SLEEP), U2.15 (VDD), U2.17 (REF), U3.1 (OUT), U3.2 (SENSE)
+12V: C8.1, C9.1, C10.1, C11.1, C17.1, C20.1, R2.2, R4.1, U2.22 (VBB1), U2.28 (VBB2), U4.P$12 (OUT)
DIR: U1.9 (PD5), U2.19 (DIR)
ENABLE~: U1.1 (PD3), U2.2 (~ENABLE)
GND: C1.2, C2.2, C3.2, C4.2, C5.2, C6.2, C9.2, C10.2, C11.2, C12.2, C13.2, C14.2, C15.2, C17.2, C18.2, C19.2, C21.2, C22.2, J1.5, JP1.6, JP2.1, R1.1, R3.1, R5.1, R7.2, R8.2, U1.3 (GND_2), U1.5 (GND_3), U1.21 (GND), U1.33 (EP), U2.3 (GND_2), U2.18 (GND), U2.29 (PAD), U3.3 (GND), U3.4 (GND), U3.6 (GND), U3.7 (GND), U3.9 (GND), U4.P$0 (GND)
MISO: JP1.1, U1.16 (PB4)
MOSI: JP1.4, U1.15 (PB3)
MS1: U1.30 (PD0), U2.9 (MS1)
MS2: U1.31 (PD1), U2.10 (MS2)
MS3: U1.32 (PD2), U2.11 (MS3)
unnamed: C6.1, U4.P$10 (TR/SS)
unnamed: C16.1, U2.4 (CP1)
unnamed: R4.2, U4.P$5 (PG)
unnamed: C5.1, U4.P$16 (INTVCC)
unnamed: R1.2, U4.P$8 (RT)
unnamed: R7.1, U2.23 (SENSE1)
unnamed: C7.1, U4.P$18 (BST)
unnamed: C7.2, L1.P$2 (2), U4.P$20 (SW)
unnamed: C20.2, U2.6 (VCP)
unnamed: C8.2, R2.1, R3.2, U4.P$11 (FB)
unnamed: L1.P$1 (1), U4.P$14 (IND)
unnamed: C16.2, U2.5 (CP2)
unnamed: R5.2, U2.13 (ROSC)
unnamed: C19.1, U2.8 (VREG)
unnamed: R8.1, U2.27 (SENSE2)
OUT1A: J1.6, U2.24 (OUT1A)
OUT1B: J1.7, U2.21 (OUT1B)
OUT2A: J1.8, U2.26 (OUT2A)
OUT2B: J1.9, U2.1 (OUT2B)
RESET~: U1.10 (PD6), U2.12 (~RESET)
RST: C22.1, JP1.5, JP2.2, R6.1, U1.29 (PC6)
SCK: JP1.3, U1.17 (PB5)
STEP: U1.2 (PD4), U2.16 (STEP)
V+: C1.1, C3.1, C4.1, J1.1, U3.5 (SHDN), U3.8 (VIN), U4.P$1 (VCC), U4.P$3 (EN)


Board: 2 copper layers, 33.2 x 35.7 mm, 38 parts (0 on the bottom side), 34 nets.

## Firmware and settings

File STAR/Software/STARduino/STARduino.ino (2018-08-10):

/* Include header */
#include "STARduino.h"

/* Instantiate objects */
ADXL375 accel;
MAX31725 tempSensor;
//VoltageSense voltageSensor;
//CurrentSense currentSensor;
BMX055_ACCEL bmxAccel;
BMX055_GYRO bmxGyro;
BMX055_MAG bmxMag;
HoneywellPressureI2C pres_sens;
//CFF_ChipCap2 chip;

/* Global variables */
char filename[16];
File dataFile;
uint32_t cycleStartTime = 0;
#define STEP_PIN 2
#define BIAS_PIN A2
uint32_t sampleRate = 5; //sample rate of the sine wave in Hertz, how many times per second the TC5_Handler() function gets called per second basically

/* Define Functions */
void setup() {
  /*
     Initalizes the STAR payload. Opens the serial connections, opens log files,
     loads queued commands, and initializes sensors.
     Inputs:
       none
     Output:
       none
     Return:
       none
  */

  
  pinMode(STEP_PIN, OUTPUT);
tcConfigure(sampleRate); //configure the timer to run at <sampleRate>Hertz
tcStartCounter(); //starts the timer
  
  SERIAL_DEBUG.begin(9600);
  Wire.begin();

  SERIAL_DEBUG.println("Began");

  // Initalize ADXL375 accel
  accel.begin();   // Not all sensors require begin() functions

  // Initalize MAX31725 tempSensor

  // Initalize VoltageSense voltageSensor

  // Initalize CurrentSense currentSensor

  // Initalize BMX055_ACCEL bmxAccel

  // Initalize BMX055_GYRO bmxGyro

  // Initalize BMX055_MAG bmxMag
  bmxMag.begin(); // Not all sensors require begin() functions

  // Initalize HoneywellPressureI2C pres_sens

  // Initalize CFF_ChipCap2 chip

  // Initialize Motor Timer

  // Initialize Bias Reader
  pinMode(BIAS_PIN, INPUT);
  analogReadResolution(12);

  // Initalize SD card
  SERIAL_DEBUG.print("Initializing SD card...");
  // see if the card is present and can be initialized:
  if (!SD.begin(PIN_SD_CS)) {
    SERIAL_DEBUG.println("Card failed, or not present");
  }
  else
  {
    SERIAL_DEBUG.println("card initialized.");
  }

  /* Find a filename that's not yet been used */
  getFreeFilename(filename);

  SERIAL_DEBUG.print("Filename: "); SERIAL_DEBUG.println(filename);

  /* open the file to write to it */
  dataFile = SD.open(filename, FILE_WRITE);

  if (dataFile) {
    /* Print file header */
    dataFile.println("MET [sec],Flag,Flag,Flag,Flag,Volt [V],Curr [A],AccelX,AccelY,AccelZ,Temp[C],AccelX,AccelY,AccelZ,BMXTemp,GyroX,GyroY,GyroZ,MagX,MagY,MagZ,Hall");
  }
  else {
    SERIAL_DEBUG.println("error opening datalog.txt");
  }

}

void loop() {//Serial.println("Working");

  if (time_for_cycle(cycleStartTime))
  {
    /* Record start of cycle */
    cycleStartTime = get_MET();

    //OUTCLR_A = (1 << PIN_LED);
    //OUTCLR_A = (1 << PIN_EXTKILL);
    //OUTCLR_A = (1 << PIN_BIAS);

    //uint16_t adcVoltageReading = voltageSensor.read_voltage();
    //uint16_t adcCurrentReading = currentSensor.read_current();

    accel.recieve_data();
    int16_t adxlAccelerometerXReading = accel.get_x_accel();
    int16_t adxlAccelerometerYReading = accel.get_y_accel();
    int16_t adxlAccelerometerZReading = accel.get_z_accel();

    tempSensor.recieve_data();
    uint16_t maximTemperatureReading = tempSensor.get_temperature();

    bmxAccel.recieve_data();
    int16_t bmxAccelerometerXReading = bmxAccel.get_x_accel();
    int16_t bmxAccelerometerYReading = bmxAccel.get_y_accel();
    int16_t bmxAccelerometerZReading = bmxAccel.get_z_accel();
    int16_t bmxAccelerometerTemperatureReading = bmxAccel.get_temp();

    bmxGyro.recieve_data();
    int16_t bmxGyroscopeXReading = bmxGyro.get_x_gyro();
    int16_t bmxGyroscopeYReading = bmxGyro.get_y_gyro();
    int16_t bmxGyroscopeZReading = bmxGyro.get_z_gyro();

    bmxMag.recieve_data();
    int16_t bmxMagnetometerXReading = bmxMag.get_x_mag();
    int16_t bmxMagnetometerYReading = bmxMag.get_y_mag();
    int16_t bmxMagnetometerZReading =  bmxMag.get_z_mag();
    uint16_t bmxMagnetometerHallReading = bmxMag.get_hall();

    //chip.readSensor();

    /*
      uint32_t portADir = PORT->Group[0].DIR.reg;
      uint32_t portBDir = PORT->Group[1].DIR.reg;
      uint32_t portAOut = PORT->Group[0].OUTSET.reg; // TODO HACK
      uint32_t portBOut = PORT->Group[1].OUTSET.reg; // TODO HACK
    */

    uint16_t biasVoltage = analogRead(A2);
    
    if ( get_MET() > (FILE_CLOSE_TIME_SEC*1000) ) {
      dataFile.close();
    }


    
    // if the file is available, write to it:
    if (dataFile) {
      dataFile.print(cycleStartTime);
      dataFile.print(",");
      /*
        dataFile.print(portADir);
        dataFile.print(",");
        dataFile.print(portBDir);
        dataFile.print(",");
        dataFile.print(portAOut);
        dataFile.print(",");
        dataFile.print(portBOut);
      */
      //dataFile.print(",");
      //dataFile.print(adcVoltageReading);
      //dataFile.print(",");
      //dataFile.print(adcCurrentReading);
      //dataFile.print(",");
      dataFile.print(adxlAccelerometerXReading);
      dataFile.print(",");
      dataFile.print(adxlAccelerometerYReading);
      dataFile.print(",");
      dataFile.print(adxlAccelerometerZReading);
      dataFile.print(",");
      dataFile.print(maximTemperatureReading);
      dataFile.print(",");
      dataFile.print(bmxAccelerometerXReading);
      dataFile.print(",");
      dataFile.print(bmxAccelerometerYReading);
      dataFile.print(",");
      dataFile.print(bmxAccelerometerZReading);
      dataFile.print(",");
      dataFile.print(bmxAccelerometerTemperatureReading);
      dataFile.print(",");
      dataFile.print(bmxGyroscopeXReading);
      dataFile.print(",");
      dataFile.print(bmxGyroscopeYReading);
      dataFile.print(",");
      dataFile.print(bmxGyroscopeZReading);
      dataFile.print(",");
      dataFile.print(bmxMagnetometerXReading);
      dataFile.print(",");
      dataFile.print(bmxMagnetometerYReading);
      dataFile.print(",");
      dataFile.print(bmxMagnetometerZReading);
      dataFile.print(",");
      dataFile.print(bmxMagnetometerHallReading);
      dataFile.print(",");
      dataFile.print(biasVoltage);
      dataFile.println();
      dataFile.flush();
      //dataFile.close(); not nessisary
      //Serial.println("Working");

    }
    // if the file isn't open, pop up an error:
    else {
      SERIAL_DEBUG.println("error opening datalog.txt");
      
    Serial.print(cycleStartTime);
      Serial.print(",");
      Serial.print(adxlAccelerometerXReading);
      Serial.print(",");
      Serial.print(adxlAccelerometerYReading);
      Serial.print(",");
      Serial.print(adxlAccelerometerZReading);
      Serial.print(",");
      Serial.print(maximTemperatureReading);
      Serial.print(",");
      Serial.print(bmxAccelerometerXReading);
      Serial.print(",");
      Serial.print(bmxAccelerometerYReading);
      Serial.print(",");
      Serial.print(bmxAccelerometerZReading);
      Serial.print(",");
      Serial.print(bmxAccelerometerTemperatureReading);
      Serial.print(",");
      Serial.print(bmxGyroscopeXReading);
      Serial.print(",");
      Serial.print(bmxGyroscopeYReading);
      Serial.print(",");
      Serial.print(bmxGyroscopeZReading);
      Serial.print(",");
      Serial.print(bmxMagnetometerXReading);
      Serial.print(",");
      Serial.print(bmxMagnetometerYReading);
      Serial.print(",");
      Serial.print(bmxMagnetometerZReading);
      Serial.print(",");
      Serial.print(bmxMagnetometerHallReading);
      Serial.print(",");
      Serial.print(biasVoltage);
      Serial.println();
    }
  }


}


/***********************************************************************************************/
// Motor Driver Interrupt Functions
// Thanks to https://gist.github.com/nonsintetic/ad13e70f164801325f5f552f84306d6f

//this function gets called by the interrupt at <sampleRate>Hertz
void TC5_Handler (void) {
  //YOUR CODE HERE
  static bool pos = 0;
  digitalWrite(STEP_PIN, pos);
  pos = !pos;
  // END OF YOUR CODE
  TC5->COUNT16.INTFLAG.bit.MC0 = 1; //don't change this, it's part of the timer code
}

/*
    TIMER SPECIFIC FUNCTIONS FOLLOW
    you shouldn't change these unless you know what you're doing
*/

//Configures the TC to generate output events at the sample frequency.
//Configures the TC in Frequency Generation mode, with an event output once
//each time the audio sample frequency period expires.
void tcConfigure(int sampleRate)
{
  // Enable GCLK for TCC2 and TC5 (timer counter input clock)
  GCLK->CLKCTRL.reg = (uint16_t) (GCLK_CLKCTRL_CLKEN | GCLK_CLKCTRL_GEN_GCLK0 | GCLK_CLKCTRL_ID(GCM_TC4_TC5)) ;
  while (GCLK->STATUS.bit.SYNCBUSY);

  tcReset(); //reset TC5

  // Set Timer counter Mode to 16 bits
  TC5->COUNT16.CTRLA.reg |= TC_CTRLA_MODE_COUNT16;
  // Set TC5 mode as match frequency
  TC5->COUNT16.CTRLA.reg |= TC_CTRLA_WAVEGEN_MFRQ;
  //set prescaler and enable TC5
  TC5->COUNT16.CTRLA.reg |= TC_CTRLA_PRESCALER_DIV1 | TC_CTRLA_ENABLE;
  //set TC5 timer counter based off of the system clock and the user defined sample rate or waveform
  TC5->COUNT16.CC[0].reg = (uint16_t) (SystemCoreClock / sampleRate - 1);
  while (tcIsSyncing());

  // Configure interrupt request
  NVIC_DisableIRQ(TC5_IRQn);
  NVIC_ClearPendingIRQ(TC5_IRQn);
  NVIC_SetPriority(TC5_IRQn, 0);
  NVIC_EnableIRQ(TC5_IRQn);

  // Enable the TC5 interrupt request
  TC5->COUNT16.INTENSET.bit.MC0 = 1;
  while (tcIsSyncing()); //wait until TC5 is done syncing
}

//Function that is used to check if TC5 is done syncing
//returns true when it is done syncing
bool tcIsSyncing()
{
  return TC5->COUNT16.STATUS.reg & TC_STATUS_SYNCBUSY;
}

//This function enables TC5 and waits for it to be ready
void tcStartCounter()
{
  TC5->COUNT16.CTRLA.reg |= TC_CTRLA_ENABLE; //set the CTRLA register
  while (tcIsSyncing()); //wait until snyc'd
}

//Reset TC5
void tcReset()
{
  TC5->COUNT16.CTRLA.reg = TC_CTRLA_SWRST;
  while (tcIsSyncing());
  while (TC5->COUNT16.CTRLA.bit.SWRST);
}

//disable TC5
void tcDisable()
{
  TC5->COUNT16.CTRLA.reg &= ~TC_CTRLA_ENABLE;
  while (tcIsSyncing());
}

 

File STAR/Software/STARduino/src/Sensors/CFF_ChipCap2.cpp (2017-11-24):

/**************************************************************************
    This library is for the GE ChipCap2 Humidity & Temperature Sensor
    
    0 ~ 100% Relative Humidity  (7 Sec. response time)
    -40 C ~ 125 C  Temperature (5 Sec. response time)
    With Low and High alarm triggers.
    
    Various models with analog and digital output @ 3.3V or 5V operation.
    
    Digi-Key Part Number: 235-1339-ND   (Digital i2c, 5V)
    Breakout Boards available at: www.circuitsforfun.com

    Written by: Richard Wardlow @ Circuits for Fun, LLC
    GNU GPL, include above text in redistribution
***************************************************************************/

#include "CFF_ChipCap2.h"
#include <Wire.h>

////////////////////////////////////////
// ChipCap2 Digital I2C Class Methods
////////////////////////////////////////
CFF_ChipCap2::CFF_ChipCap2(uint8_t addr)
{
    _i2caddr = addr;
}

// Initiate the Wire library and join the I2C bus 
void CFF_ChipCap2::begin(void)
{
    Wire.begin(_i2caddr);
    status = 0;
}

// Configure which pin is used for the ChipCap2 Power pin and set as output
void CFF_ChipCap2::configPowerPin(uint8_t pwrpin)
{
    _pwrpin = pwrpin;
    pinMode(_pwrpin, OUTPUT);
}

// Configure which pin is used for the ChipCap2 Ready pin and set as input
void CFF_ChipCap2::configReadyPin(uint8_t readypin)
{
    _readypin = readypin;
    pinMode(_readypin, INPUT);
}

// Configure which pin is used for the ChipCap2 Alarm Low pin and set as input
void CFF_ChipCap2::configAlarmLowPin(uint8_t alowpin)
{
    _alowpin = alowpin;
    pinMode(_alowpin, INPUT);
}

// Configure which pin is used for the ChipCap2 Alarm High pin and set as input
void CFF_ChipCap2::configAlarmHighPin(uint8_t ahighpin)
{
    _ahighpin = ahighpin;
    pinMode(_ahighpin, INPUT);
}

// If using the pwrpin for powering chipcap use this function to turn it on or off
void CFF_ChipCap2::power(uint8_t onOff)
{
    if(_pwrpin != NULL)
    {
        if(onOff == 0)
            digitalWrite(_pwrpin, LOW);
        
        if(onOff == 1)
            digitalWrite(_pwrpin, HIGH);
    }
}

// Check the ChipCap2 Ready pin to see if conversion is complete
bool CFF_ChipCap2::dataReady(void)
{
    uint8_t val;
    
    val = digitalRead(_readypin);
    if ( val == 0)
        return false;
    if (val == 1)
        return true;

}

// Check for Alarm Low Trigger
bool CFF_ChipCap2::checkAlarmLow(void)
{
    uint8_t val;
    
    val = digitalRead(_alowpin);
    if ( val == 0)
        return false;
    if (val == 1)
        return true;
}

// Set Alarm Low Trigger Value in Celsius
void CFF_ChipCap2::setAlarmLowVal(int16_t alarmlowon)
{
    readSensor();
    if (status == CCF_CHIPCAP2_STATUS_COMMANDMODE)
    {
        uint16_t alowon, alowoff;
        uint8_t lowByte, hiByte;
        int8_t alarmlowoff = alarmlowon + 1;
        alowon = ((alarmlowon + 40) * 99);
        lowByte = alowon & 255;
        hiByte = alowon >> 8;
        Wire.beginTransmission(_i2caddr);
        Wire.write(0x5A);
        Wire.write(hiByte);
        Wire.write(lowByte);
        Wire.endTransmission();
        delay(2);
        alowoff = ((alarmlowoff + 40) * 99);
        lowByte = alowoff & 255;
        hiByte = alowoff >> 8;
        Wire.beginTransmission(_i2caddr);
        Wire.write(0x5B);
        Wire.write(hiByte);
        Wire.write(lowByte);
        Wire.endTransmission();
        delay(2);
    }
}

int16_t CFF_ChipCap2::getAlarmLowVal()
{
    readSensor();
    if (status == CCF_CHIPCAP2_STATUS_COMMANDMODE)
    {
        uint8_t edat[3];
        int16_t eALow;
        Wire.beginTransmission(_i2caddr);
        Wire.write(0x1A);
        Wire.write(0);
        Wire.write(0);
        Wire.endTransmission();
        delay(1);
        Wire.beginTransmission(_i2caddr);
        Wire.requestFrom((uint8_t)_i2caddr, (uint8_t)3, (uint8_t)true);
        edat[0] = Wire.read();
        edat[1] = Wire.read();
        edat[2] = Wire.read();
        Wire.endTransmission();
        eALow = (((edat[1] << 8) + (edat[2])) / 99) - 40; 
        return eALow;
    }
}

// Check for Alarm High Trigger
bool CFF_ChipCap2::checkAlarmHigh(void)
{
    uint8_t val;
    
    val = digitalRead(_ahighpin);
    if ( val == 0)
        return false;
    if (val == 1)
        return true;
}

// Set Alarm High Trigger Value in Celsius
void CFF_ChipCap2::setAlarmHighVal(int16_t alarmhighon)
{
    readSensor();
    if (status == CCF_CHIPCAP2_STATUS_COMMANDMODE)
    {
        uint16_t ahion, ahioff;
        uint8_t lowByte, hiByte;
        int8_t alarmhighoff = alarmhighon - 1;
        ahion = ((alarmhighon + 40) * 99);
        lowByte = ahion & 255;
        hiByte = ahion >> 8;
        Wire.beginTransmission(_i2caddr);
        Wire.write(0x58);
        Wire.write(hiByte);
        Wire.write(lowByte);
        Wire.endTransmission();
        delay(2);
        ahioff = ((alarmhighoff + 40) * 99);
        lowByte = ahioff & 255;
        hiByte = ahioff >> 8;
        Wire.beginTransmission(_i2caddr);
        Wire.write(0x59);
        Wire.write(hiByte);
        Wire.write(lowByte);
        Wire.endTransmission();
        delay(2);
    }
}

int16_t CFF_ChipCap2::getAlarmHighVal()
{
    readSensor();
    if (status == CCF_CHIPCAP2_STATUS_COMMANDMODE)
    {
        uint8_t edat[3];
        int16_t eAHigh;
        Wire.beginTransmission(_i2caddr);
        Wire.write(0x18);
        Wire.write(0);
        Wire.write(0);
        Wire.endTransmission();
        delay(1);
        Wire.beginTransmission(_i2caddr);
        Wire.requestFrom((uint8_t)_i2caddr, (uint8_t)3, (uint8_t)true);
        edat[0] = Wire.read();
        edat[1] = Wire.read();
        edat[2] = Wire.read();
        Wire.endTransmission();
        eAHigh = (((edat[1] << 8) + (edat[2])) / 99.29) - 40; 
        return eAHigh;
    }
}

// Enters command mode (Only valid during first 10ms after power-on)
void CFF_ChipCap2::startCommandMode(void)
{
    if (_pwrpin != NULL)
    {
        power(0);
        delay(50);
        power(1);
        delay(2);
    }
    Wire.beginTransmission(_i2caddr);
    Wire.write(0xA0);
    Wire.write(0);
    Wire.write(0);
    Wire.endTransmission();
    delay(5);
    readSensor();
}

// Enters normal mode of operation
void CFF_ChipCap2::startNormalMode(void)
{
    Wire.beginTransmission(_i2caddr);
    Wire.write(0x80);
    Wire.write(0);
    Wire.write(0);
    Wire.endTransmission();
    delay(5);
    readSensor();
}

// Read Humidity and Temperature Sensor Data
void CFF_ChipCap2::readSensor(void)
{
    uint8_t rht[4];
    
    Wire.beginTransmission(_i2caddr);
    Wire.requestFrom((uint8_t)_i2caddr, (uint8_t)4, (uint8_t)true);
    rht[0] = Wire.read();
    rht[1] = Wire.read();
    rht[2] = Wire.read();
    rht[3] = Wire.read();	
    Wire.endTransmission();
    status = rht[0] >> 6;
    humidity = (((rht[0] & 63) << 8) + rht[1]) / 163.84;
    temperatureC = (((rht[2] << 6) + (rht[3] / 4)) / 99.29) - 40; 
    temperatureF = temperatureC * 1.8 + 32;
}
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

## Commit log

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2017-10-17 STEP of CAD
    STEP file of the cad with colored safe zone on plate
    [assemblywithcameras.stp]
2017-10-17 STARduino I2C fixes
    [Arm Link Body.prt, Arm Link Cover.prt, BasePlate (1).prt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]
2017-10-25 Added the new layout for the plater
    [PlateLayout.stp]
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2017-11-03 datalogger eagle and NX
    [datalogger.brd, datalogger.prt, datalogger.sch]
2017-11-05 Add files via upload
    Added FOV for Pi Cams obtained from GrabCad
    [platelayoutwFOVv1.stp]
2017-11-06 scamp and shaker
    added scamp range of motion approximately. added new shaker mechanism
    with motors
    [CDR_Plate_Layout.stp]
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2017-11-07 reorganized cad files
    moved cad files to cad folder and created folder for pdr
    [Arm Link Cover.prt, Central Housing.prt, Electronics Box V2.prt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]
2017-11-07 Add files via upload
    Placeholders for stuff
    [MotorDriver Board.prt, VBias.prt]
2017-11-07 Add files via upload
    layout w/ pi zeros and datalogger
    [platelayoutCOMPDRv2.stp]
2017-11-07 added pi zeroes and data logger
    [platelayoutCOMPDRV3.stp]
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2017-11-11 STAR EBox Altered and Added to plate.
    [newerbox448651.prt, platelayoutCOMPDRV3_stp.prt]
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2017-11-14 added constraints moved starduino
    [platelayoutCOMPDRV3_stp.prt]
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2017-11-19 made changes to ebox
    [newerbox448651.prt, platelayoutCOMPDRV3_stp.prt]
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2017-11-19 added fasteners to pdr folder
    [19155A340_304 STAINLESS STEEL CORNER BRACKET.prt, 92125A130_TYPE 18-8 SS FLAT-HEAD SOCKET CAP SCREW.prt, 92290A751_TYPE 316 SS SOCKET HEAD CAP SCREW.prt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]
2017-11-19 some changes to baseplate and ebox
    [BasePlate (1)484648.prt, newerbox448651.prt, platelayoutCOMPDRV3_stp.prt]
2017-11-19 LED board, added text
    [LED_Driver.brd, LED_Driver.sch]
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2017-11-20 added usb flash drives
    [mini_usb.prt, platelayoutCOMPDRV3_stp.prt]
2017-11-20 humidity sensor to STARduino
    [starduino.brd, starduino.sch]
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2017-11-21 small fixes to get code to compile
    [STARduino.ino]
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2017-11-27 LED FOV and moved stuff
    [LED FOV.prt, LED_Board.prt, PlateLayout.stp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]
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2017-12-01 continued renaming of parts and reassociation of assemblies with new part names
    [LED_Board.prt, PiCamwithsilicon.prt, SCAMP_To_Scale_stp.prt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]
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2017-12-04 shortened pi heat block
    [HeatBlockforPi.prt]
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2017-12-06 uploaded some fasteners swapped screws on pizeros
    [93925A220_TYPE 18-8 SS INTERNAL-TOOTH LOCK WASHER.prt, 94205A101_TYPE 316 STAINLESS STEEL NYLON-INSERT LOCKNUT.prt, RaspberryPiZeroWAssembly.prt]
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2017-12-06 fixed routing shit on datalogger:
    [datalogger.brd, datalogger.sch]
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2017-12-23 fixed datalogger USB port
    [bias_generator.brd, bias_generator.sch, datalogger.brd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]
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2018-01-08 Updated to final end effector shape, added O-ring seals for housings.
    [Central Housing.prt, Pitch Motor Housing V2.prt, SCAMP To Scale.prt]
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2018-01-30 NASA Update
    Starting to update the design for the NASA requirements. Will go over more in person, and the CAD is not finished yet, I just have to get to homework tonight. If there are questions let me know.
    [DoveEffector.prt, EndCap.prt, MassMotor.prt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]
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2018-02-11 Added holes for boards and shaker to baseplate
    [92125A134_TYPE 18-8 SS FLAT-HEAD SOCKET CAP SCREW.prt, 92290A060_TYPE 316 SS SOCKET HEAD CAP SCREW.prt, BasePlate.prt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]
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2018-02-11 LIghtening payload process has begun. Also integrating all the technology needed for our new goals. I am going to continue working on this throughout the next day and a half and have everyting ready 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
    [077_step.prt, 106_step.prt, 112_step.prt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]
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2018-02-13 All of SCAMP CAD updated- Only things left to complete are the mounting holes for contacts and electronics box as well as bolts for those. SCAMP inlcudes motor, drive shaft, harmonic drive and mass d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
    Will also create mass slide tomorrow.
    [077_step.prt, 106_step.prt, 112_step.prt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]
2018-02-13 Did things to baseplate to solve wave linking issue
    [BasePlate.prt]
2018-02-13 Added more holes and some weight reduction. Motor is now accurately massed and all that is left to do is potentially change some colors and add holes and bolts for the contacts. Mechanical drawings a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
    [074.STEP, 074_step.prt, BasePlate.prt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]
2018-02-13 fixed duplicates
    [BasePlate.prt, TERP_payload.prt]
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2018-03-27 Starting to update to new and lighter mass movement system
    [Central Housing.prt, DoveEffector.prt, SCAMP Flight.prt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]
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2018-04-06 Updated with linear motion carriage for mass movement
    [Ball Plunger.prt, Mass Shuttle.prt, bearing shaft.prt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]
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2018-04-20 cam for first half of test tube holder
    [Untitled.f3d, tubeholder.f3d]
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2018-06-08 Fixed sunshade fastener holes
    [LEDsilicone.prt, TERP_payload.prt, new_sunshade.prt]
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2018-06-09 updated shaker disk and link arm
    will now use a set screw and an oil bearing for easier machening
    [link_arm.prt, shaker_disk.prt]
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2018-07-07 Fixed the three terminal capacitor routing (five capacitors).
    [Power.brd, Power.sch]
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2018-07-08 Added analog isolator to bias and revised connector
    [bias_generator.sch]
2018-07-08 fixed choke routing on power board
    [Power.brd, Power.sch, starduino.brd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]
2018-07-08 Finished routing new bias board rev 2.0. Fixed the choke configuration on that board.
    [bias_generator.brd, bias_generator.sch]
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2018-07-08 I think I fixed all of the GSE_GND being '+3V3_FILT' but I don't know how that happened in the first place
    [Power.brd, Power.sch]
2018-07-08 Fixed Blaire's nonsense on the power board. No longer shorting 3V3 to GSE_GND. The input names still make no sense
    [Power.brd, Power.sch]
2018-07-08 Fixed all the wire stubs on Starduino
    [starduino.brd, starduino.sch]
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2018-07-09 New inductors for the power board, changed the error message on the values script and added CBEs. Because who needs sleep
    [Power.brd, Power.sch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]
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2018-07-22 Updated bias board and libraries to reflect the actual package used by the analog isolator
    [bias_generator.brd, bias_generator.sch]
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2018-07-22 Fixed an air wire on the ground lines and a non-connection in the sketch
    [Power.brd, Power.sch]
2018-07-22 starduino shield for M0 becuase custom boards don't always work
    [shield.brd, shield.sch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]
2018-07-23 Fixed optoisolator circuit and added SPI header on top, but not yet the SPI head on the ICSP board. Fixed a lot of air wires
    [shield.brd, shield.sch]
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2018-07-24 STARduino sheild. Updated holes, resistor size, added some names to components to make assembly easier
    [shield.brd, shield.sch]
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2018-07-29 Added new holes for Arduino M0 and slide rod tapped holes
    [BasePlate.prt]
2018-08-06 M0_PreFlight2018
    Writes more than one line to file now. Closes data logging file after a time
    [SunShadeBottom1to1.prt, new_sunshade.prt]
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2018-08-30 fixes to cad
    [91771A830_18-8 SS FLAT HEAD PHILLIPS MACHINE SCREW_10-32_.625.prt, BasePlate.prt, TERP_payload.prt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]
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2018-10-20 adding renders and some changes I noticed I didnt push yet
    [StarMotor.prt, TERP_payload.prt, holderhalf_top.prt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]

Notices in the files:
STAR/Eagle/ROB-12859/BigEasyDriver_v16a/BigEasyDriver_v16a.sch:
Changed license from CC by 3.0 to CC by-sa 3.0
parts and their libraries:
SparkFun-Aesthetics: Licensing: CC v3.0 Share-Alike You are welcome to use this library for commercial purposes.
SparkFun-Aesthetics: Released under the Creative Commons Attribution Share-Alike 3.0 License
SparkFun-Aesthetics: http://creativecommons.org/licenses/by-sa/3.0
